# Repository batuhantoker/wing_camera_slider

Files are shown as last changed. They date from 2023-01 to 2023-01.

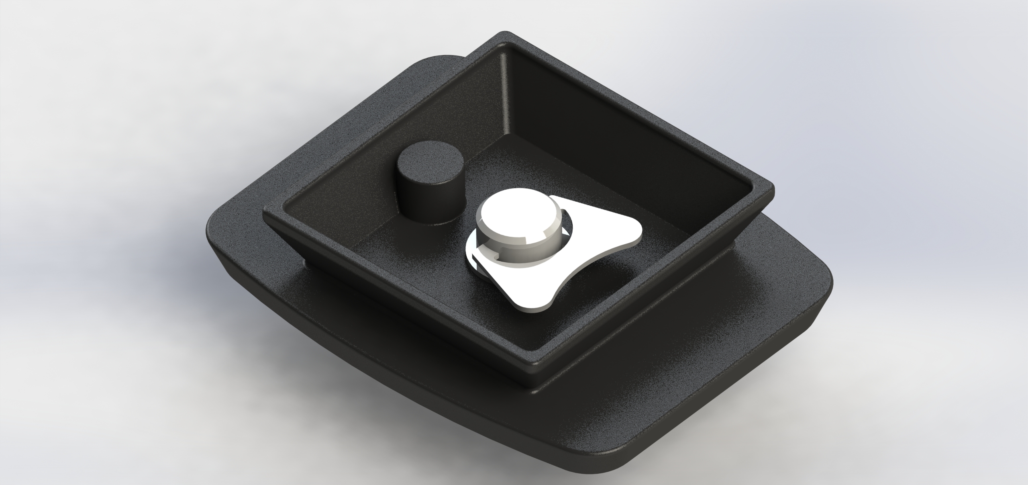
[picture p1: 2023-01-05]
CAD/tripod/Yeni klasör/Tripod Mount Bottom.JPG

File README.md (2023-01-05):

# wing_camera_slider
Kinematic analysis, simulation and CAD files of two link planar robotic arm based on one actuator wing mechanism.

There is a report in the files (mechanism, kinematic analysis, design of components, material selection, CAD design, control and image processing)
MATLAB codes for kinematic and dynamic analysis are also provided.

# Simulations

ezgif com-gif-maker (1)
ezgif com-gif-maker

# CAD design







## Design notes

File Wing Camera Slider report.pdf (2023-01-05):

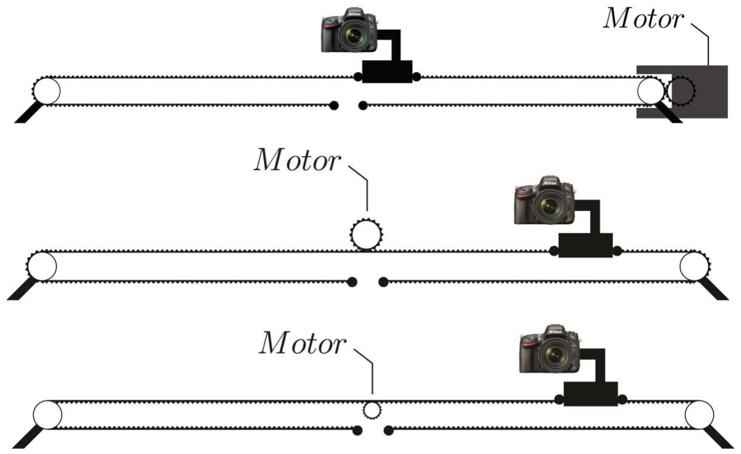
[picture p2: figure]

Figure 1

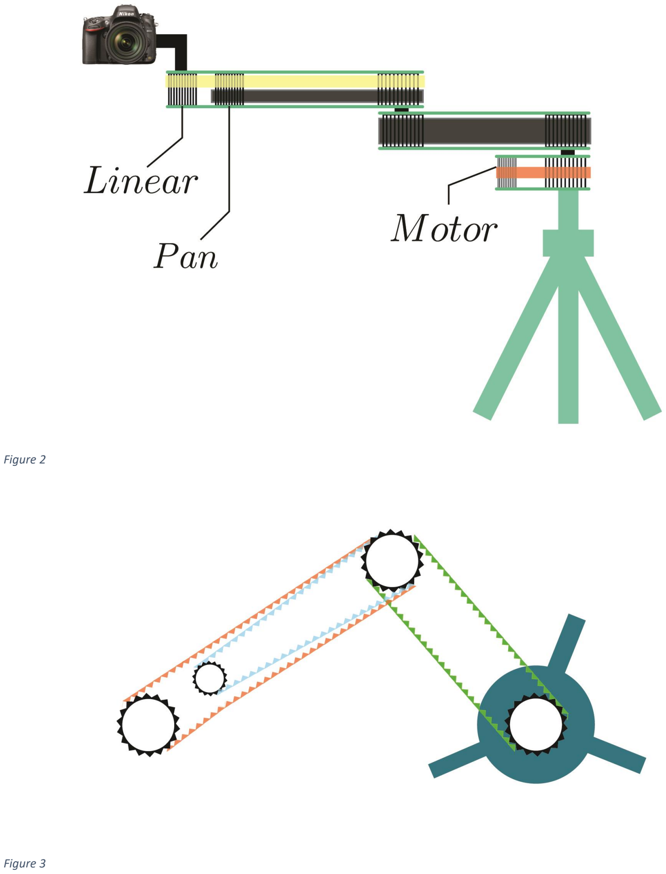
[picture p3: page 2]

Figure 2

Figure 3

Figure 4

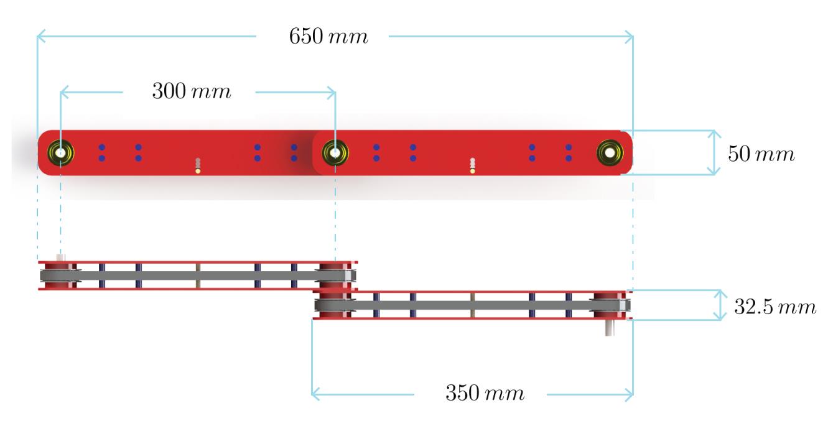
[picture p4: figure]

### 1. Analysis

Kinematic Analysis

Kinematic analysis applied on the mechanism that is represented in figure. m1 and m2 are the masses of links respectively. Links have lengths of L1 and L2. End points of link 1 is defined as (x1, y1, z1), and (x2, y2, z2) is the end point of link 2. The aim of this kinematic analysis is to obtain τθ1

and τθ2

for given inputs of m, L, θ̇ and θ̈. f1 and f2 are forces needed to obtain the motion. Newton’s second law of motion states that;

f = ma

In this mechanism, forces f1 and f2 can be defined as;

f1 = [

fx1
fy1
fz1

] = m1 [
ẍ1
ÿ1
z1̈

]

and
f2 = [

fx2
fy2
fz2

] = m2 [
ẍ2
ÿ2
z̈2

]

Points presented in figure can be written as a function of L1 , L2, θ1and θ2; for link 1 → {

x1 = L1x cosθ1
y1 = L1x sinθ1
z1 = 0
for link 2 → {

x2 = L1x cosθ1 + L2x cosθ2 y2 = 0
z2 = 0
Time derivative of the positions will be

x1̇ = −L1x sinθ1x θ̇
1
ẏ1 = L1x cosθ1xθ̇
1
z1̇ = 0
and

ẋ2 = −L1x sinθ1x θ̇

1−L2x sinθ2x θ̇
2
ẏ2 = 0
ż2 = 0
And then the directional accelerations of the given system is; ẍ1 = −L1x cosθ1x θ̇²

1−L1x sinθ1x θ̈
1
ÿ1 = L1x sinθ1xθ̇²

1−L1x cosθ1x θ̈
1
z1̈ = 0
and
ẍ2 = −L1x sinθ1x θ̈

1−L1x cosθ1x θ̇²

1−L2x sinθ2x θ̈

2−L2x cosθ2x θ̇²
2
ÿ2 = 0
z̈2 = 0
These accelerations are substituted into Newton’s second law of motion f1 = [

fx1
fy1
fz1

] = m1 [
−L1x cosθ1x θ̇²

1−L1x sinθ1x θ̈
1
L1x sinθ1xθ̇²

1−L1x cosθ1x θ̈
1
0

]

f2 = [

fx2
fy2
fz2

] = m2 [
−L1x sinθ1x θ̈

1−L1x cosθ1x θ̇²

1−L2x sinθ2x θ̈

2−L2x cosθ2x θ̇²
2
0
0

]

The torques needed to obtain the motion can be found by torque matrix that is obtained by using free-body-diagrams
τθi = [

τθ1
τθ2

] = [

τθ2 − f1xL1xsinθ1 + f1xL1xcosθ1 −f2xL2xsinθ2 − f2xL2xcosθ2

]

And, so that velocity squared is

v

2
1 = ẋ

2
1 + ẏ

2
1
v

2
2 = ẋ

2
2 + ẏ

2
2

so directional velocity of each link is v1 = √(−L1x sinθ1x θ̇
1)

2 + (L1x cosθ1xθ̇
1)

2

v2 = √(−L1x sinθ1x θ̇
1−L2x sinθ2x θ̇
2)

2

And angular velocity can be found by using directional velocity and length of links;

v1 = ω1xL1
v2 = ω2xL1
By using these one can obtain ω1 =

v1
L1

and
ω2 =

v2
L2
Power needed to run this system will be; P1 = τθ1

xω1
P2 = τθ2

xω2
The numerical values of torque at each joint can be obtained with this analysis for given inputs of mass, length of links, velocity of the system, and acceleration of the system. CAD simulation will provide information of mass of each link, then by defining minimum time required to complete the linear movement, maximum torque needed will be computed. The mass of the link 1 is selected as 0.8 kg, and mass of link 2 with camera is selected as 3.8 kg. Then torque/position of θ1 graph is given in the FİGURE with units of kg*cm.

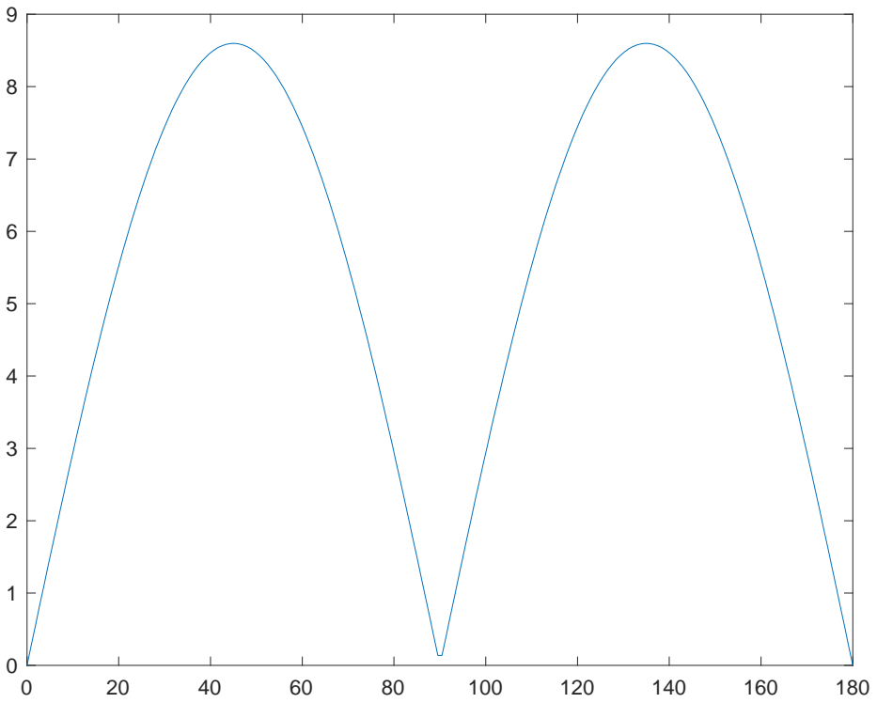
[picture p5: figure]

And then torque/position of θ2 graph is shown in the FİGURE

## Angle(degree)

## Torque at joint 1(kg*cm)

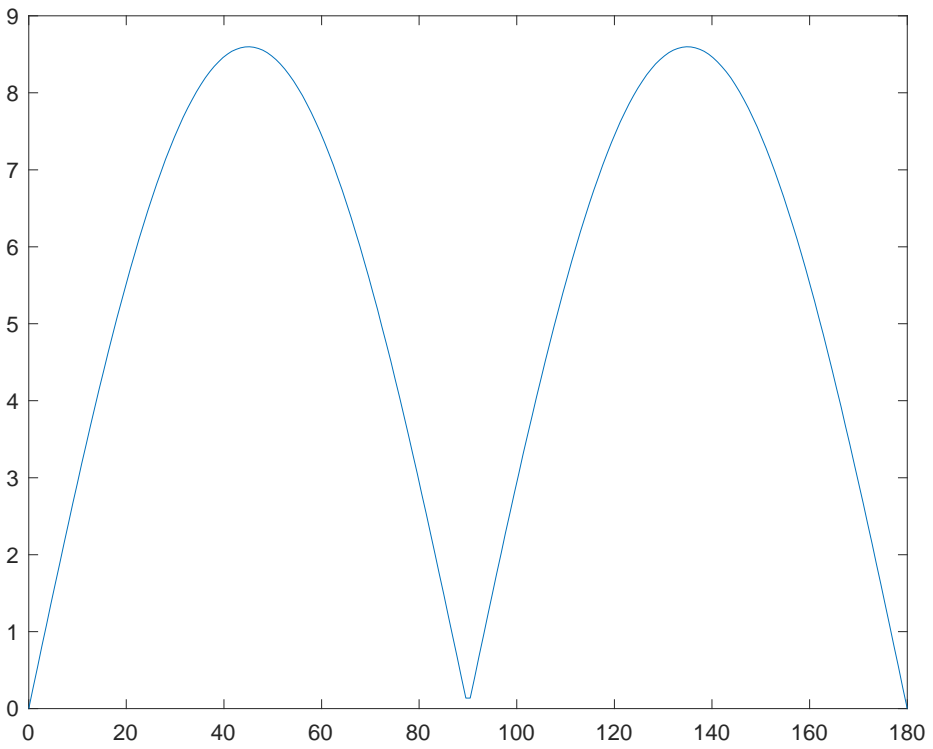
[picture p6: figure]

Since the all torque will be provided by one motor, we can select required torque as given in the FİGURE. Total torque needed to run the system is τ = τθ1 + τθ2

## Angle(degree)

## Torque at joint 2(kg*cm)

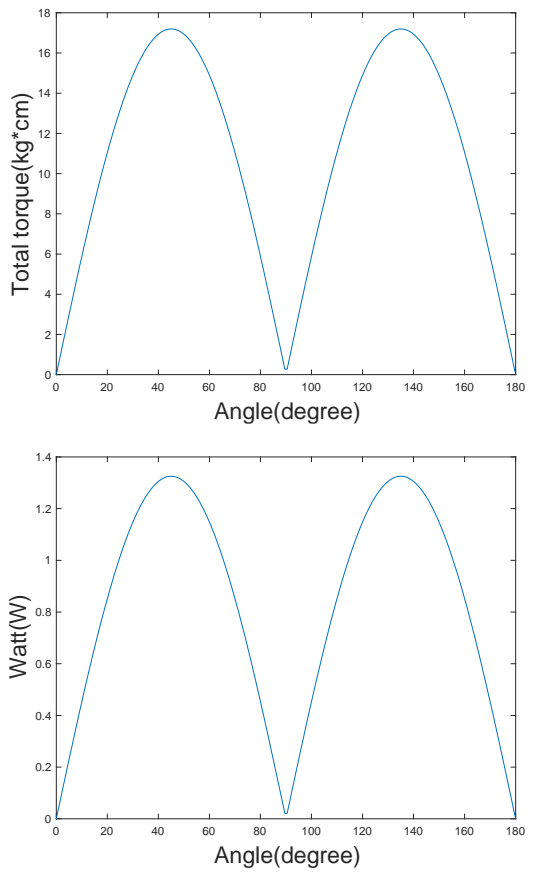
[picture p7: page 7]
Angle(degree); Watt(W)

Total torque(kg*cm)

Belt-Pulley System
Maximum tension Tmax at the belt can be calculated with the formula of

Tmax =

2.5 τmax
Pd
where Pd is the pitch diameter. τmax = 1.6876Nm
τ(lbfin) = 8.85x τ(Nm)

Tmax =

37.33815
Pd
Tpeak = TmaxxService factor τdesign = τmaxxService factor

Service factor is chosen as 1.5 as recommended value
SPD/SI A 6A53-021DF0608 was selected as pulley which has Pd value of 0.79 in. Which is 0.020066m.Then peak tension force is
Tpeak = 79.88 lbf
And design torque is
τdesign = 2.53Nm
3 mm GT2 seems a reliable at small number of revolution per minute according to the FİGURE appendix

To choose a belt design power will be used
Pd = PtxService factor
so the design power will be
Pd = 0.00198375kW
Belt will be thickness of 6 mm and material of Nylon Covered, Fiberglass Reinforced, Neoprene. This belt’s breaking strength is 158 N per 1 mm belt width. For 6 mm thickness, breaking strength will be ~950N and that is higher than Tpeak = 79.88 lbf~350N

Bearing selection
Bearings are the machine parts that can be used for reducing friction between moving parts, thus in this design 8 SKF 7200 BEP was used to get rid of energy losses. SKF 7200 has the dimensions of d 10 mm D 30 mm B 9 mm d 1 18.3 mm d 2 14.57 mm D 1 22.85 mm a 13 mm r 1,2 min. 0.6 mm r 3,4 min. 0.3 mm which are represented in FİGURE

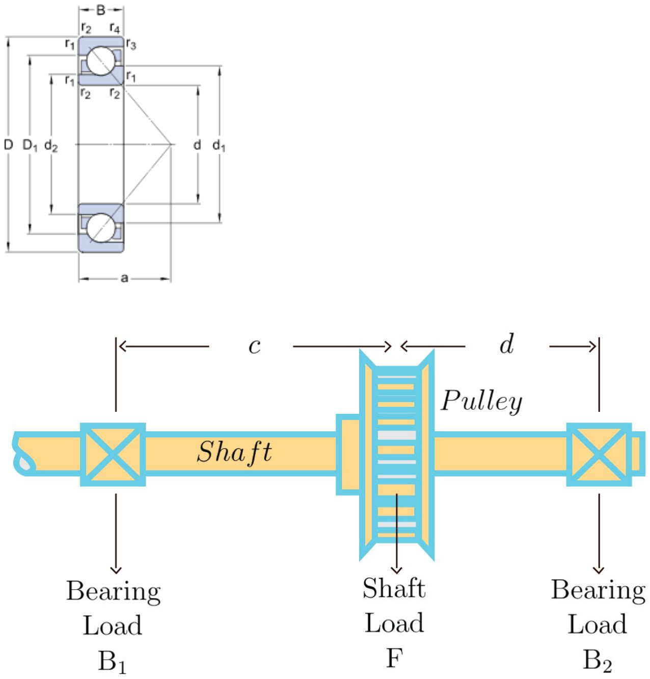
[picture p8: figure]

B1 =

Fd
(c + d)

B2 =

Fc
(c + d)
c = d

B1 = B2 =

F
2

Loads on the bearings are calculated by the peak tension on the pulley and relative positions of bearings with respect to pulley. In the design, components are aligned on
a shaft as two bearings and one pulley between them with equal distance. Therefore, loads are distributed between bearings equally as shown in the equations above. According to calculated loads bearings are selected for the mechanism that withstand the required forces.

Motor selection
Required torque is 2.53Nm~25kgcm which is given as τdesign in previous parts. JX Servo PDI-HV5932MG was selected because it can provide up to 32.3 kgcm with 8.4 V. 6V operating speed can provide up to 25.2 kgcm stall torque.
Battery selection
The wing slider is expected to operate for an hour approximately for convenience. The selected motor JX Servo PDI-HV5932MG, is able to generate 2 Nm torque by using 2480 mA at 6.6 V at locked position (stall current).
The BeagleBone Rev C, is using 460 mA at 5 V,
Battery Life = Battery Capacity in Milli amps per hour / Load Current in Mill amps * 0.70 =>Battery Capacity in Milli amps per hour = Battery Life * Load Current in Mill amps / 0.70 1*(2480+460)/0.75
Battery Capacity (mAh) = Device Consumption (mA) * 0.75
2480+460=3920 mAh

By considering the market products, 4000 mAh Li-Po battery would be sufficient to operate the mechanism for an hour without stopping. As it will not operate continuously under the normal conditions, the slider can work more than an hour with the designed specifications.

*The factor of 0.75 makes allowances for external factors which can affect battery life.

Material selection
Materials used in the wing slider are selected with considering the lightweight construction of the mechanism, required torque and force capacity of the parts and minimizing the deflection of the camera within the motion path. For the links, pulleys are made of aluminum alloy and for the bearings and supporters between links stainless steel is used.
FEM Analysis

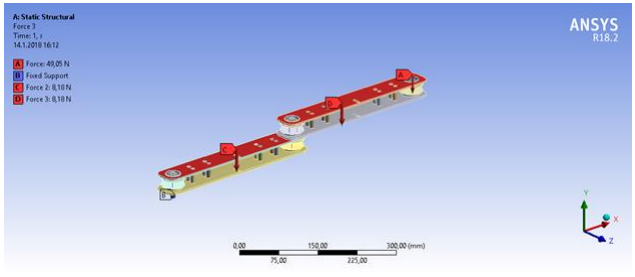
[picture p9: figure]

Structural analysis of the slider done by using ANSYS. Materials are defined as aluminum for the links and pulleys, stainless steel for bearings and the supporter pins between the links. To obtain maximum deformation and stresses, mechanism is fully extended. By considering weight of the camera as 5 kg, 49.05 N force is applied from the attachment of camera to the mechanism. Weight of the camera is calculated as 1,6681 kg with the defined materials and forces are applied from the center of the each link.

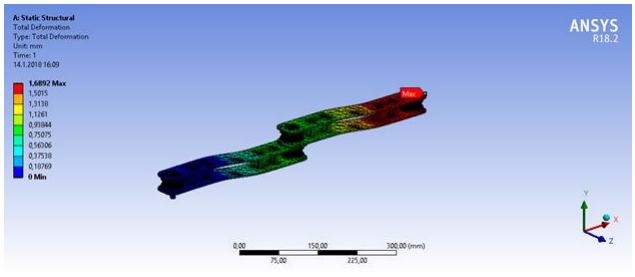
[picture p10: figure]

Results reveal that 1,69 mm total displacement occurs at the end of the top link. In order to decrease displacement, link thicknesses were increased from 3 mm to 4 mm. By changing the initial design 0,96 mm total displacement achieved at the end of the fully extended mechanism.

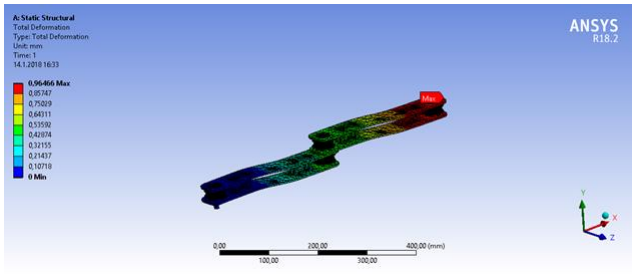
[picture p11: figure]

### 2. CAD Design

CAD design is done with SolidWorks. The dimensions were selected with respected to belt-pulley

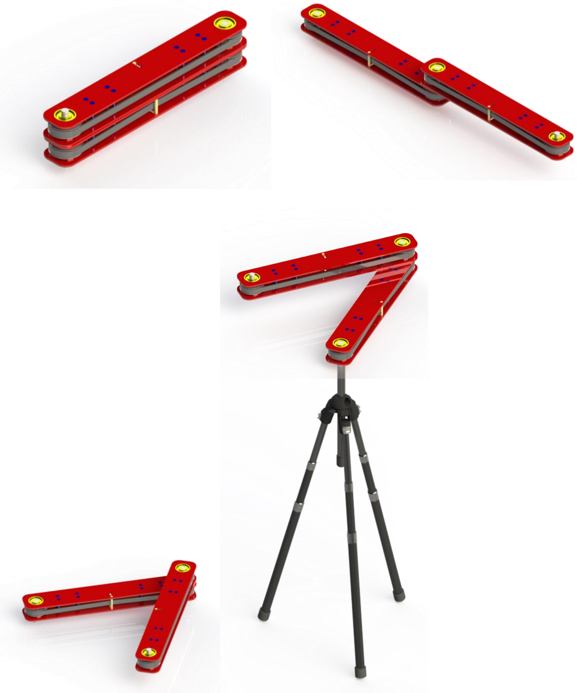
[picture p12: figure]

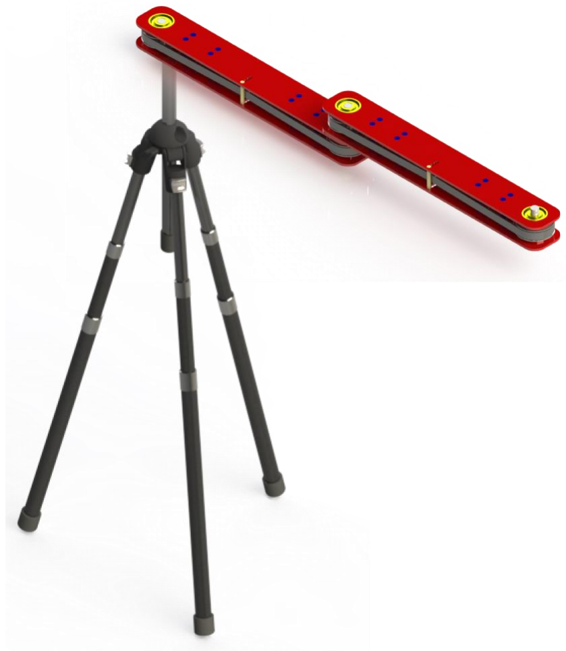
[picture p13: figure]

### 3. Control

A mathematical algorithm was constructed on MATLAB to obtain required values of torques at each link. The MATLAB code is presented in the appendix. This MATLAB code will use the data obtained by image processing to do the control.

### 4. Image processing

Framework Selection
Although there are plenty of others, MATLAB and OpenCV are two most common frameworks/software used for image processing. OpenCV is way too faster than the MATLAB in terms of image processing. MATLAB is built upon Java and Java is built upon C. Therefore, its path through low level language is complicated than the Python, which is OpenCV built upon. At the end, while MATLAB lets you to process 4-5 frames per second, OpenCV can process 30 frames per second, which is more than enough for real time image processing. On top of that, OpenCV is specifically made for image processing, and does have full support from the community and can run even on 64 MB of rams, the only issue is the memory leaks, that can be handled easily.

Board Selection
BeagleBone Black Rev C is a popular embedded computer for internet of things (IoT) applications. It has 1 GHz processor, and 512 MB RAM, which can handle low FPS image processing with any lag behind. Furthermore, it has 4 GB on-board embedded Multi-Media Controller, that is enough for average image processing applications. However, the biggest advantage of BeagleBone is its expansion abilities with 65 digital and 7 analog-to-digital controllers. Therefore, BeagleBone Black Rev C is selected for image processor board.

Development of a Prototype Object Detection Application
To further test the capabilities of OpenCV and also our competency to develop an image processing / machine learning capable IoT project, a small-medium sized code has been written. The packages imutils, numpy, argparse, time and OpenCV are used for the development of the project. As pre-trained model is needed for the software, MobileNet SSD pre-trained model with convolutional neural network, therefore machine learning integrated model has been used thanks to its fast and reliable real-time multiple detection abilities.

Output

The software has been tested on using a single body object per frame, to determine its ability to detect object in real time. The figure below tells the program is able to identify the object as bottle with confidence level of 99.64%, and tells the user to move the camera right to center the object’s right and left boundaries into center of the frames.

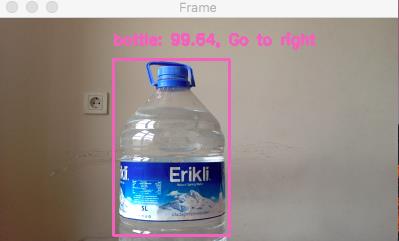
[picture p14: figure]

Figure 5 - OpenCV output of realtime video

As in another example, the software is able to identify the train, and commands user to move left the camera, and when it is centered tell to stay in its current position.

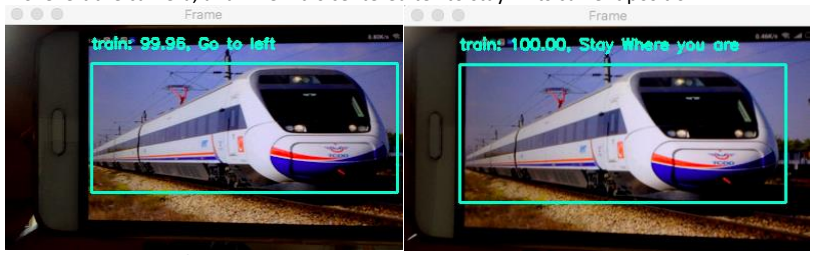
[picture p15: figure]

Figure 6 - OpenCV output of object placement

After the first successful attempts, the software has been tested on multiple objects in frames. From the figures below, it can be seen that it is able to identify the objects correctly, however, the confidence level is either low or the object are missing to be identified with small errors. The main reason is the illumination for the specific examples. Therefore, we can conclude that, to get successful and reliable results from OpenCV, we need to operate under the well-illuminated conditions.

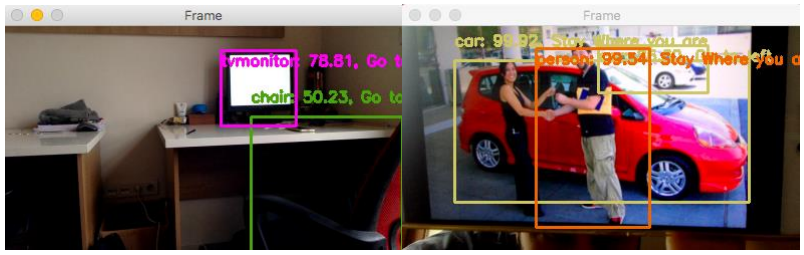
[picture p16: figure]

Figure 7 - OpenCV analysis on multiple objects

### 5. Conclusion

To conclude up, a wing slider design for a slider has been chosen by the company. Furthermore, instead of mechanical panning, it has been decided to use image processing unit on top of camera, to put an extra value to the slider by adding not existing product specifications in the market.

### 6. References

http://www.skf.com/group/products/bearings-units-housings/ball-bearings/angular-contact-ball-bearings/single-row-angular-contact-ball-bearings/single-row/index.html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 (http://www.skf.com/group/products/bearings-units-housings/ball-bearings/angular-contact-ball-bearings/single-row-angular-contact-ball-bearings/single-row/inde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) https://www.banggood.com/JX-Servo-PDI-HV5932MG-30KG-Large-Torque-360-High-Voltage-Digital-Servo-p-1074871.html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 (https://www.banggood.com/JX-Servo-PDI-HV5932MG-30KG-Large-Torque-360-High-Voltage-Digital-Servo-p-1074871.html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) https://www.digikey.com/en/resources/conversion-calculators/conversion-calculator-battery-life (https://www.digikey.com/en/resources/conversion-calculators/conversion-calculator-battery-life)
http://www.chd.hk/UploadFiles/Att/201701191006295.pdfhttps://www.learnopencv.com/embedded-computer-vision-which-device-should-you-choose/ (https://www.learnopencv.com/embedded-computer-vision-which-device-should-you-choose/)

### 7. Appendix

Figures

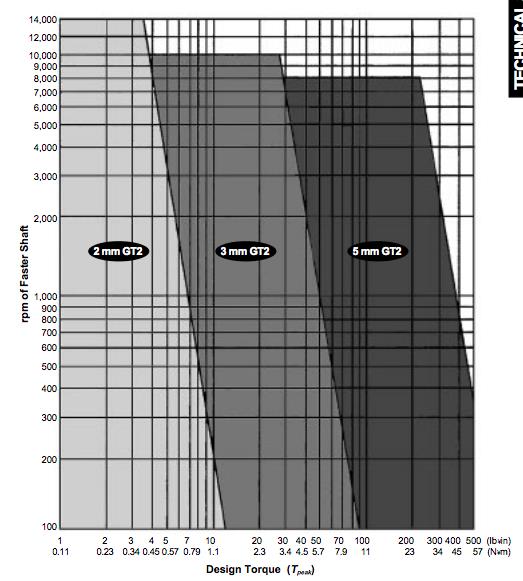
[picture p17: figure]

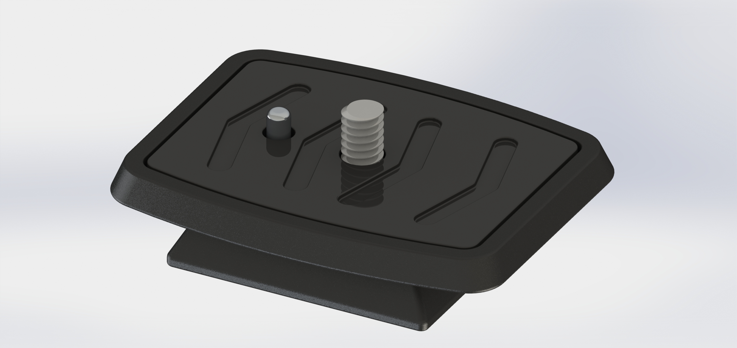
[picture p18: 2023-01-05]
CAD/tripod/Yeni klasör/Tripod Mount Top.JPG

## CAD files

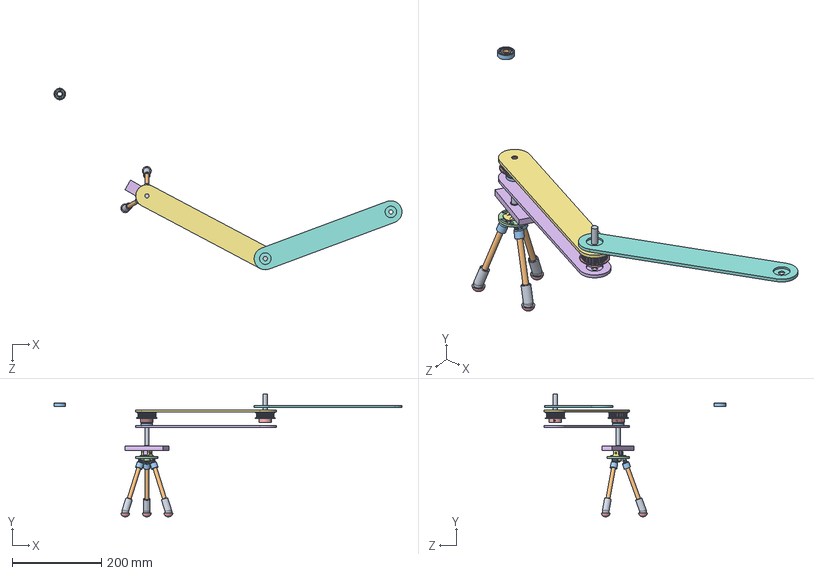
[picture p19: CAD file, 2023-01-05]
CAD/tripod/Assem1.SLDASM
779.1 x 274.6 x 406.5 mm
1-4 20 Latch Screw
Shaft
6000_PART1 x 3
6000_PART2 x 3
6000_PART3 x 21
Link1_alt
Link2_alt
shaft_2

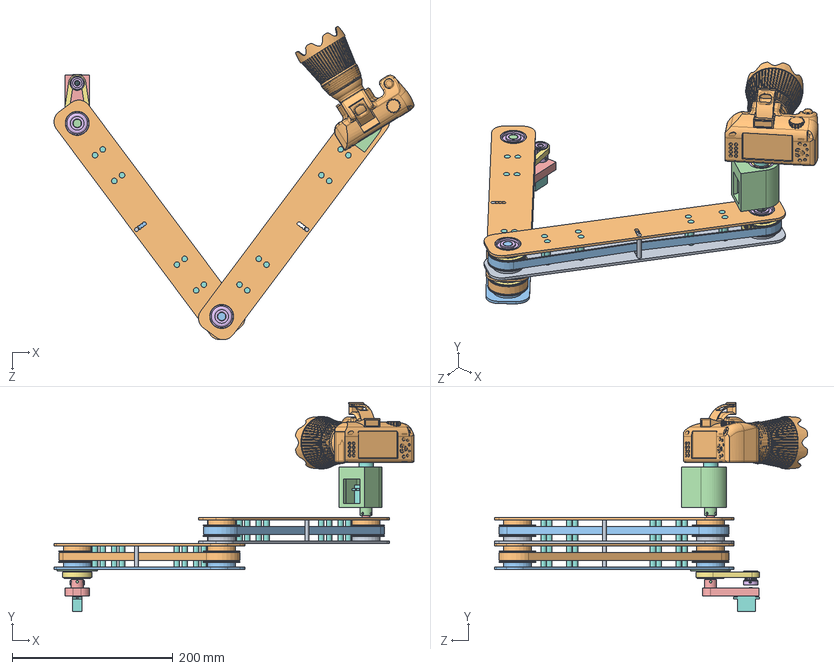
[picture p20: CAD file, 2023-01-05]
CAD/Camslider.SLDASM
447.8 x 260.3 x 389.8 mm
Bottom link
Top link x 2
Gear shaft
Tripod shaft
Cam shaft
angular contact ball bearing_68_skf x 8
gear x 4
Support pin x 16
Belt pin x 2
Belt2-1^Camslider
Belt3-2^Camslider
Camera_Platform
7200 BEP_PART1
7200 BEP_PART2
7200 BEP_PART3 x 9
Shaft
1-4 20 Latch Screw
camera
Bottom link1
Link pulley
Motor_holder
Motor_pulley
Belt5-3^Camslider
Servo Motor (SG90) x 2

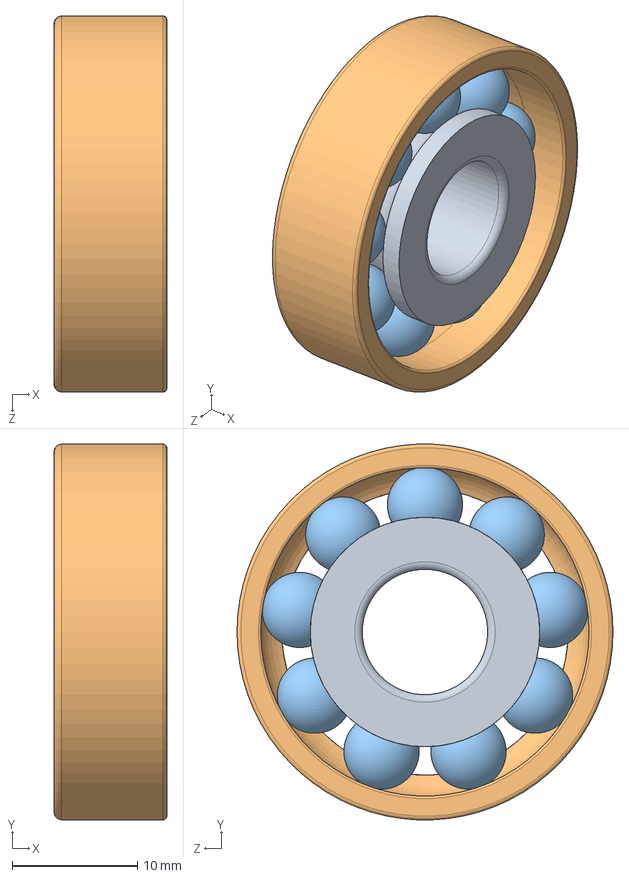
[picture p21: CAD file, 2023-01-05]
CAD/Bearing/7200 BEP.sldasm
9.00 x 30.0 x 30.0 mm
7200 BEP_PART1
7200 BEP_PART2
7200 BEP_PART3 x 9

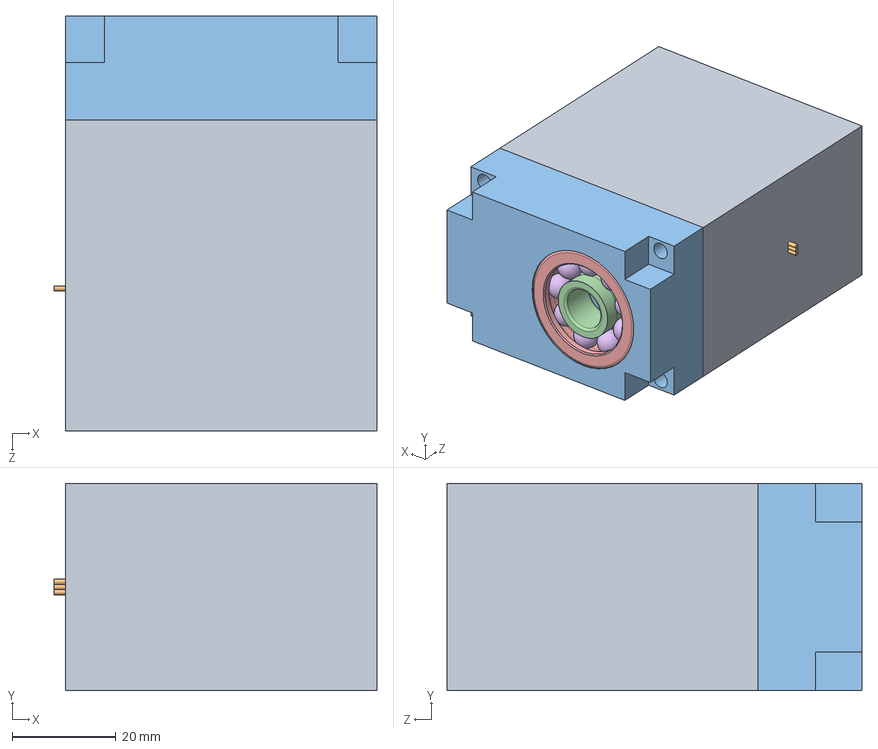
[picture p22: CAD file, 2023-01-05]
CAD/Motor part/camera_assembly.SLDASM
62.2 x 40.0 x 80.0 mm
camera_motor
POWERHD AR-3606HB
Camera_Platform
7200 BEP_PART1
7200 BEP_PART2
7200 BEP_PART3 x 9

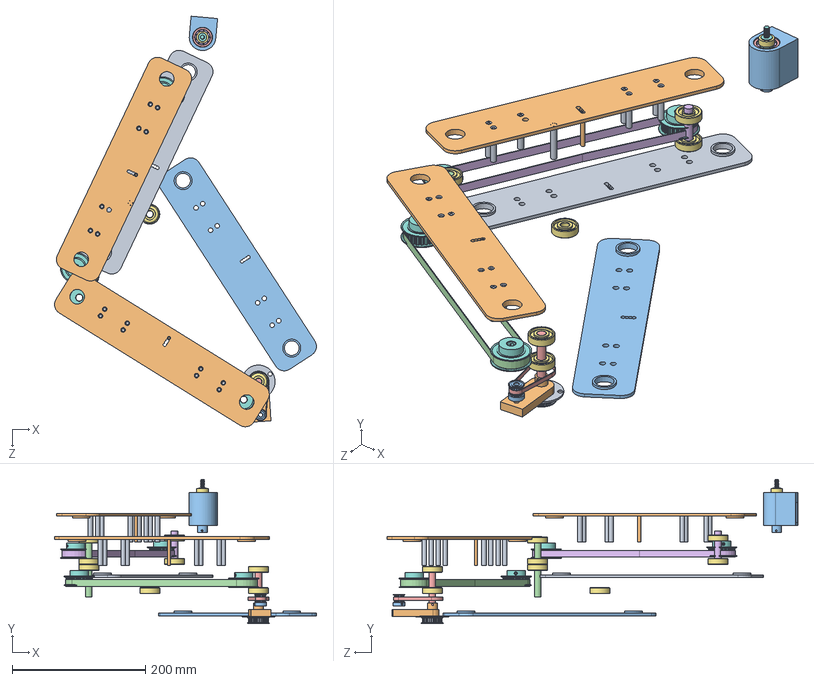
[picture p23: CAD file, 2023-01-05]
CAD/Camera Slider.SLDASM
393.7 x 216.5 x 617.2 mm
Bottom link
Top link1 x 2
Bottom link1
Gear shaft
Tripod shaft
Cam shaft
angular contact ball bearing_68_skf x 8
gear x 4
Support pin x 16
Belt pin x 2
Camera_Platform
7200 BEP_PART1
7200 BEP_PART2
7200 BEP_PART3 x 9
Shaft
1-4 20 Latch Screw
Link pulley
Motor_holder
Motor_pulley
Belt1-1^Camera Slider
Belt3-3^Camera Slider
Belt4-4^Camera Slider

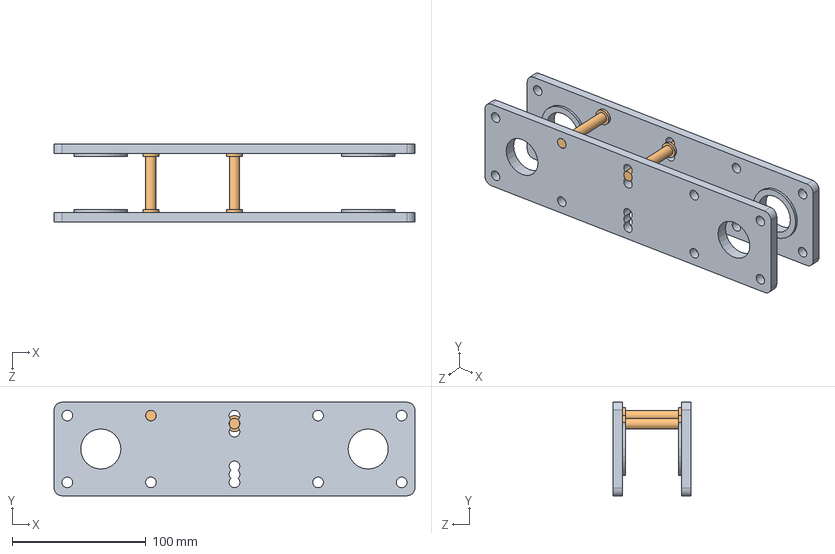
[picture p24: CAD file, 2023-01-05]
CAD/Son/Assem1.SLDASM
270.0 x 70.0 x 58.0 mm
Bottom x 2
Pin x 2

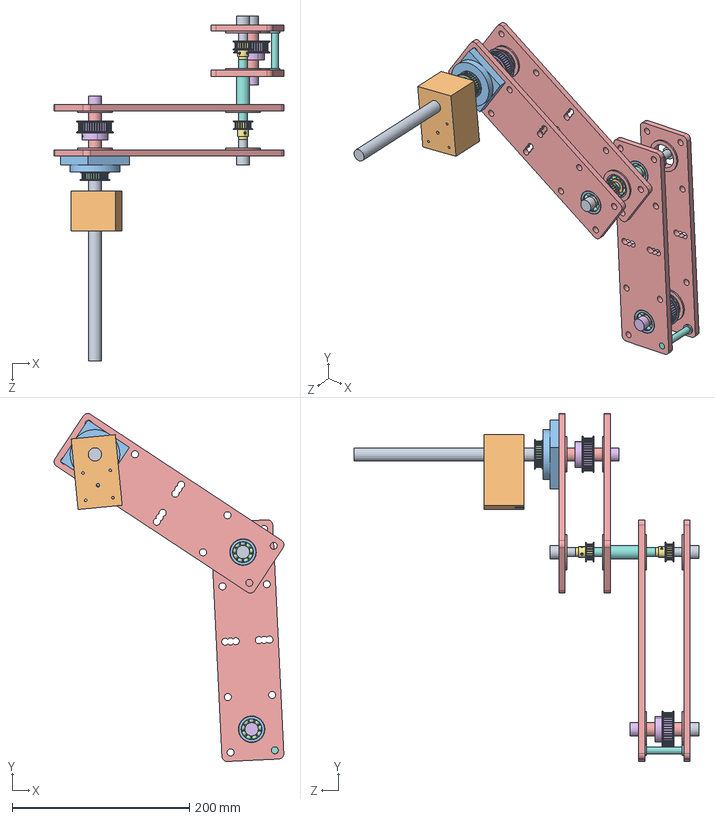
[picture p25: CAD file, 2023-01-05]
CAD/Son/Assem2.SLDASM
259.3 x 392.4 x 389.0 mm
Shaft1
Motor holder
motorsabitleyici
32teeth
Bottom x 4
40teeth x 2
10teeth x 2
Pin
Shaft6 x 3
7200 BEP_PART1 x 7
7200 BEP_PART2 x 7
7200 BEP_PART3 x 63
Shaft3 x 2
Shaft7 x 2
Shaft8 x 2
Shaft4

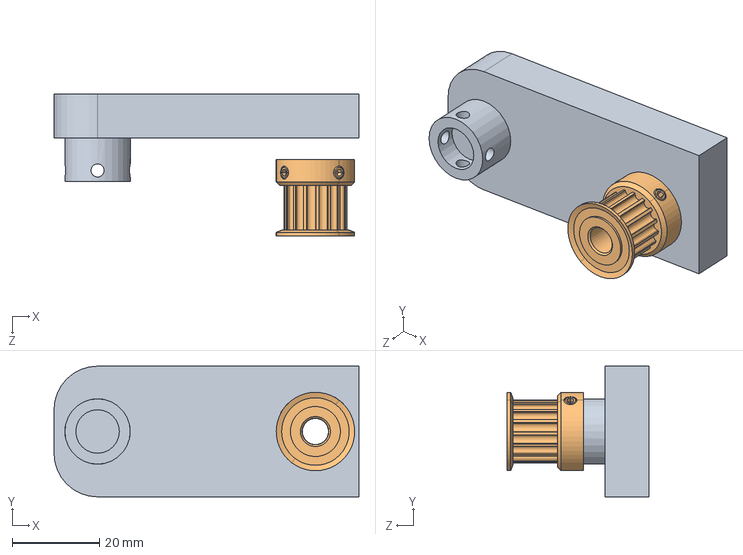
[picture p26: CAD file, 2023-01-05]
CAD/Motor.SLDASM
70.0 x 30.0 x 32.5 mm
Motor_holder
Motor_pulley

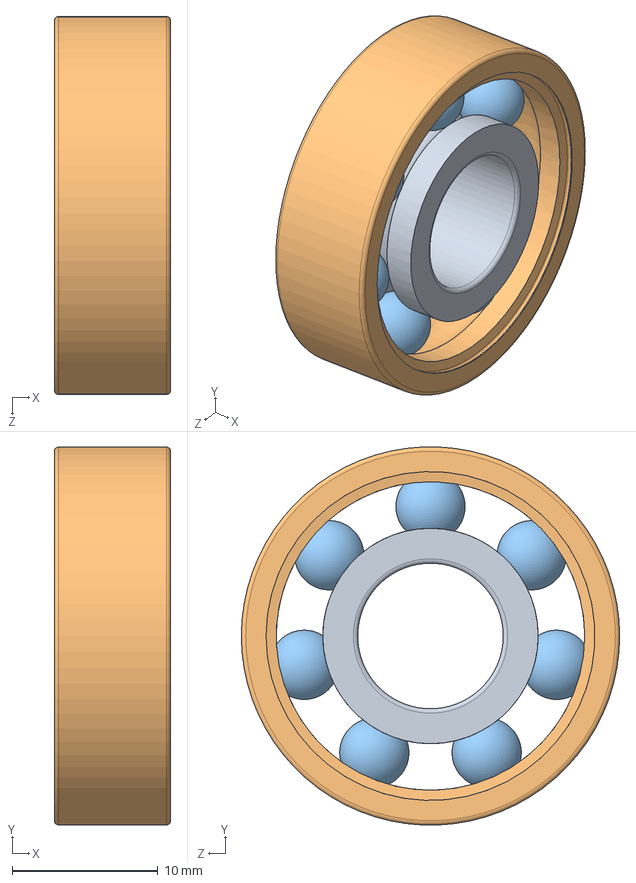
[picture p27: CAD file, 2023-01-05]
CAD/Son/6000.sldasm
8.00 x 26.0 x 26.0 mm
6000_PART1
6000_PART2
6000_PART3 x 7

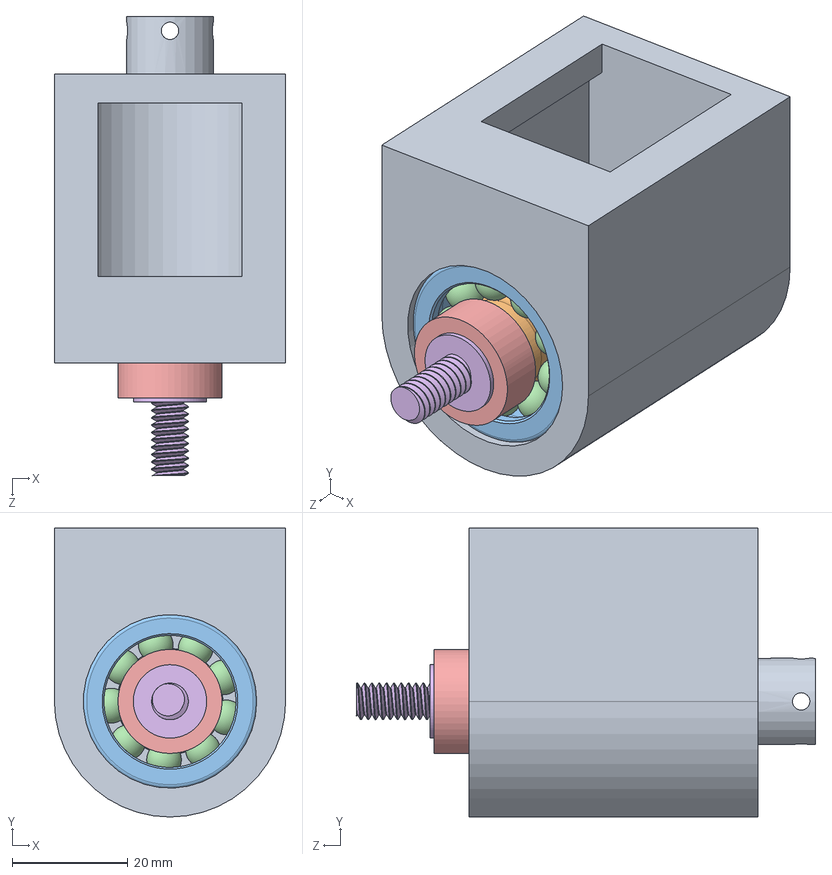
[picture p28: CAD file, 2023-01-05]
CAD/Camera System.SLDASM
40.0 x 50.0 x 79.5 mm
Camera_Platform
7200 BEP_PART1
7200 BEP_PART2
7200 BEP_PART3 x 9
Shaft
1-4 20 Latch Screw

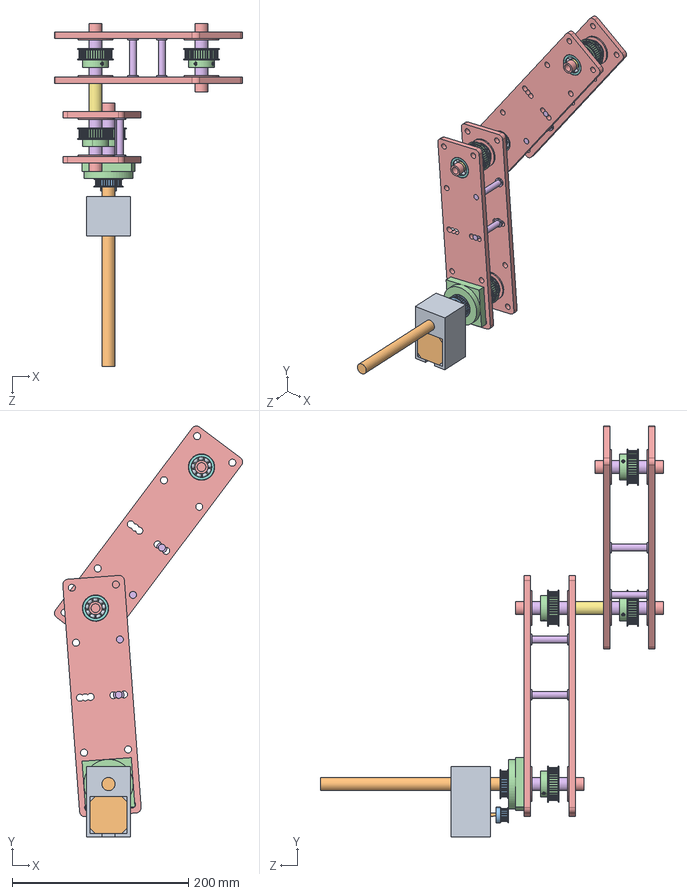
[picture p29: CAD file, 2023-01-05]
CAD/Son/Assem.SLDASM
213.3 x 465.9 x 389.0 mm
Motor holder
42BYG Stepper Motor.stp
SDP_a_6a53m016df0606.stp
motorsabitleyici
Bottom x 4
Pin x 4
7200 BEP_PART1 x 8
7200 BEP_PART2 x 8
7200 BEP_PART3 x 72
Shaft1
32teeth
40teeth x 4
Shaft2 x 5
Shaft3 x 4
Shaft4

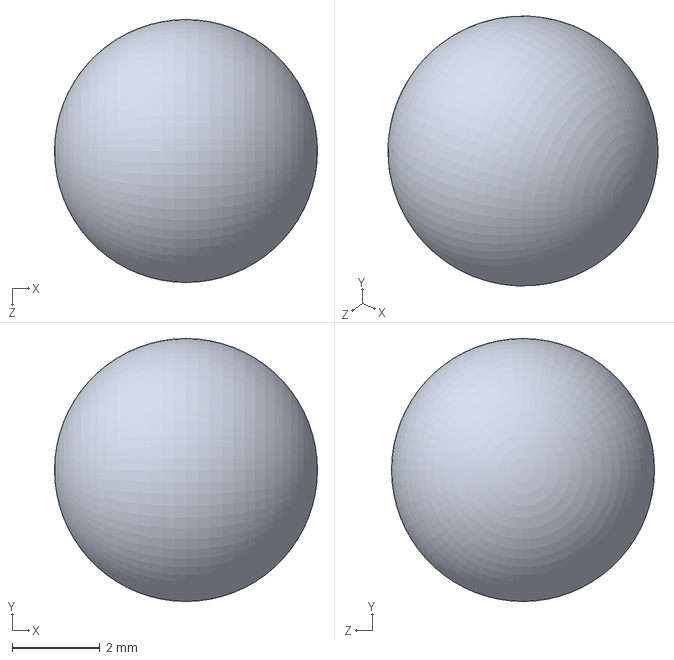
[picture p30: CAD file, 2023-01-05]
CAD/Bearing/7200 BEP_PART3.sldprt
6.00 x 6.00 x 6.00 mm

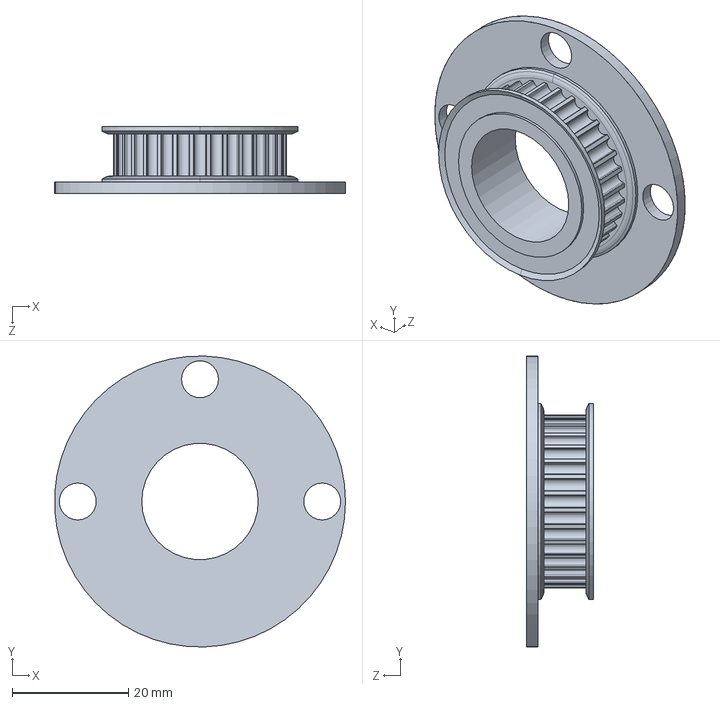
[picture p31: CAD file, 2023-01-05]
CAD/Link pulley.SLDPRT
50.0 x 50.0 x 11.5 mm

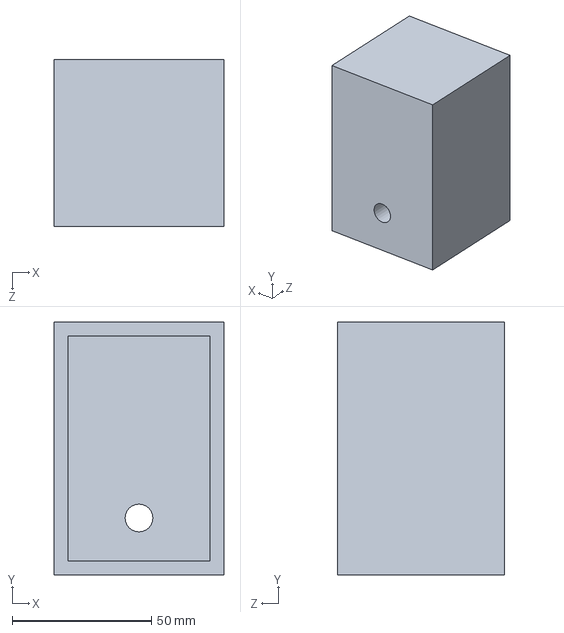
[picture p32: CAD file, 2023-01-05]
CAD/Motor part/Holder cover.SLDPRT
61.0 x 91.0 x 60.0 mm

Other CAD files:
CAD/Son/Pin.SLDPRT
CAD/tripod/Yeni klasör/Tripod Camera Mount.SLDPRT
CAD/Yeni klasör/Gear3.SLDPRT
CAD/1-4 20 Latch Screw.SLDPRT
CAD/Bearing/7200 BEP_PART1.sldprt
CAD/Bearing/7200 BEP_PART2.sldprt
CAD/Belt pin.SLDPRT
CAD/Bottom link.SLDPRT
CAD/Bottom link1.SLDPRT
CAD/Cam shaft.SLDPRT
CAD/Camera_Platform.SLDPRT
CAD/Gear shaft.SLDPRT
CAD/Motor part/42BYG Stepper Motor Bracket.stp
CAD/Motor part/42BYG Stepper Motor.stp
CAD/Motor part/Camera_Platform.SLDPRT
CAD/Motor part/POWERHD AR-3606HB.SLDPRT
CAD/Motor part/SDP_a_6a53m032df0606.stp
CAD/Motor part/camera_motor.SLDPRT
CAD/Motor part/motorsabitleyici.STL
CAD/Motor part/motorsabitleyici2.SLDPRT
CAD/Motor_holder.SLDPRT
CAD/Motor_pulley.SLDPRT
CAD/Servo Motor (SG90).SLDPRT
CAD/Shaft.SLDPRT
CAD/Son/10teeth.SLDPRT
CAD/Son/16teeth.SLDPRT
CAD/Son/16teeth.stp
CAD/Son/32teeth.SLDPRT
CAD/Son/40teeth.SLDPRT
CAD/Son/40teeth.stp
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
